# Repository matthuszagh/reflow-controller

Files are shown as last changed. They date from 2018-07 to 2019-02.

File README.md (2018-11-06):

A reflow oven controller, based on Henrik Forsten's project whose source code is found
[here](https://github.com/Ttl/reflow-controller). More in-depth documentation can be found in the
documentation subdirectory. The microcontroller code heavily leverages the [LUFA USB framework
code](http://www.fourwalledcubicle.com/LUFA.php).

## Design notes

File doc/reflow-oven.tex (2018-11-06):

\documentclass[11pt,twoside,a4paper]{report}
\setlength\parindent{0pt}
\usepackage{fullpage}
\usepackage{hyperref}
\hypersetup{
    colorlinks=true,
    linkcolor=black,
    urlcolor=blue,
}
\usepackage{mathtools}
\usepackage{booktabs}
\usepackage{ltablex}
\usepackage{amssymb}
\usepackage{graphicx}
\usepackage{tabularx}
\usepackage{gensymb}
\usepackage{pdfpages}
\usepackage{amsmath}
\usepackage{bm}
\usepackage{listings}
\usepackage{color}
\usepackage{float}
\usepackage[makeroom]{cancel}
\DeclareMathOperator{\csch}{csch}
\setlength\fboxrule{.3mm}
\DeclarePairedDelimiter\ceil{\lceil}{\rceil}
\DeclarePairedDelimiter\floor{\lfloor}{\rfloor}

\definecolor{dkgreen}{rgb}{0,0.6,0}
\definecolor{gray}{rgb}{0.5,0.5,0.5}
\definecolor{mauve}{rgb}{0.58,0,0.82}

\lstset{frame=tb,
  showstringspaces=false,
  columns=flexible,
  frame=none,
  basicstyle={\small\ttfamily},
  numbers=left,
  xleftmargin=.67cm,
  keywordstyle=\color{blue},
  commentstyle=\color{dkgreen},
  stringstyle=\color{mauve},
  breaklines=true,
  breakatwhitespace=true,
  tabsize=4
}

\def\dbar{{\mathchar'26\mkern-12mu d}}

\begin{document}

\tableofcontents

\section{Reflow Oven}

\subsection{Introduction}

\textit{Status: Functional}\newline

To do:
\begin{enumerate}
\item Review and understand microcontroller code.
\item Review and understand pc code.
\end{enumerate}

Building a homemade reflow oven will serve several benefits: (1) it will allow me to make PCBs in
the future with greater accuracy and less development time, and (2) it will give me a sense of how
to program, interact with and generally use microcontrollers to build embedded computers that have
less demanding performance constraints than is required when FPGAs are needed. FPGAs are often
overkill and many things can be done with a simple and cheap microcontroller. Additionally,
microcontrollers can often be used as a way to interface between an FPGA and a host computer.

\subsection{Materials \& Overview}

\subsubsection{Repository}
The repository for this project is at
\href{run:/home/matt/developer/reflow-controller}{/home/matt/developer/reflow-controller}. It
includes hardware design files as well microcontroller and host computer code. This project is taken
from Henrik Forsten, documented online
\href{http://hforsten.com/toaster-oven-reflow-controller.html}{here}.

\subsubsection{Hardware}
In addition to the materials specified by the hardware files, this also requires an ISP programmer
which is necessary to set fuse bits on the AVR microcontroller and also makes programming it
easier. The programmer can also be used in the future on any further AVR microcontroller. I am using
\href{https://www.sparkfun.com/products/9825}{this one}. The ISP uses an SPI interface to configure
the ATMega8U2 microcontroller. One of these pins is VCC that can be used to feed a 5V power supply
from the ISP to the reflow board. This feature can be toggled on and off using the power target
switch shown in Figure~\ref{fig:isp-power-switch}. Since that power line also connects to the
thermocouple ADC which can only support a max voltage of 4V, we must ensure that the power switch is
set to ``No Power'' before connecting the ISP to the AVR. In retrospect, it would have been much
better to route the header to VBUS instead of VCC which would have allowed us to use the ISP to
power the device.

\begin{figure}[h]
  \centering
  
  \caption{The ISP power switch. ``Power Target'' will route 5V to the AVR and ``No Power'' will not
    route a signal to the AVR.}
  \label{fig:isp-power-switch}
\end{figure}

\subsubsection{Microcontroller Software}
Programming the AVR is done with \href{http://www.fourwalledcubicle.com/LUFA.php}{LUFA}, which in
turn depends on \href{https://www.nongnu.org/avrdude/}{AVRDUDE} and
\href{https://dfu-programmer.github.io/}{DFU-Programmer} as well as
\href{https://www.microchip.com/webdoc/AVRLibcReferenceManual/index.html}{AVR Libc}. The AVR code
uses a PID controller to control the operation of a solid state relay attached to the oven (PWM) and
attempts to converge the measured temperature to the target temperature at each time instant.

\subsubsection{Host Computer Software}
The host computer code is written in Python (don't forget to activate the VirtualENV environment
when using it) in the code repository. It listens at the serial port /dev/ttyACM0 and plots the
temperature readings from the AVR. It isn't strictly necessary, but is very useful especially since
the oven is too slow to match the temperature profile and some additional interactive steps must be
taken such as insulating the oven and opening the door during cool-down.

\subsection{Methods}

\subsubsection{Schematic}
The schematic for the controller is shown in Figure~\ref{fig:reflow-controller-sch}. The main
component on this board is an
\href{http://ww1.microchip.com/downloads/en/DeviceDoc/doc7799.pdf}{ATMega8u2 microcontroller} from
Atmel. The microcontroller has built-in support for USB communication and 8k bytes of flash
memory. It is clocked by an 8MHz external clock (which is necessary for USB functionality) and is
powered at 3.3V. In order to correctly power the device we externally supply the power in one of 2
ways: (1) connect a 5V supply to VBUS via the J5 connector, or (2) allow the host PC to provide the
5V over the USB connection. The second alternative should be preferred in most scenarios, since we
will generally plot the output of the PID controller to the host computer. In both instances, the 5V
power supply is downregulated via an onboard regulator,
\href{https://www.diodes.com/assets/Datasheets/AP2127.pdf}{AP2127K}, to the 3.3V used by the
microcontroller.\newline

\begin{figure}[h]
  \centering
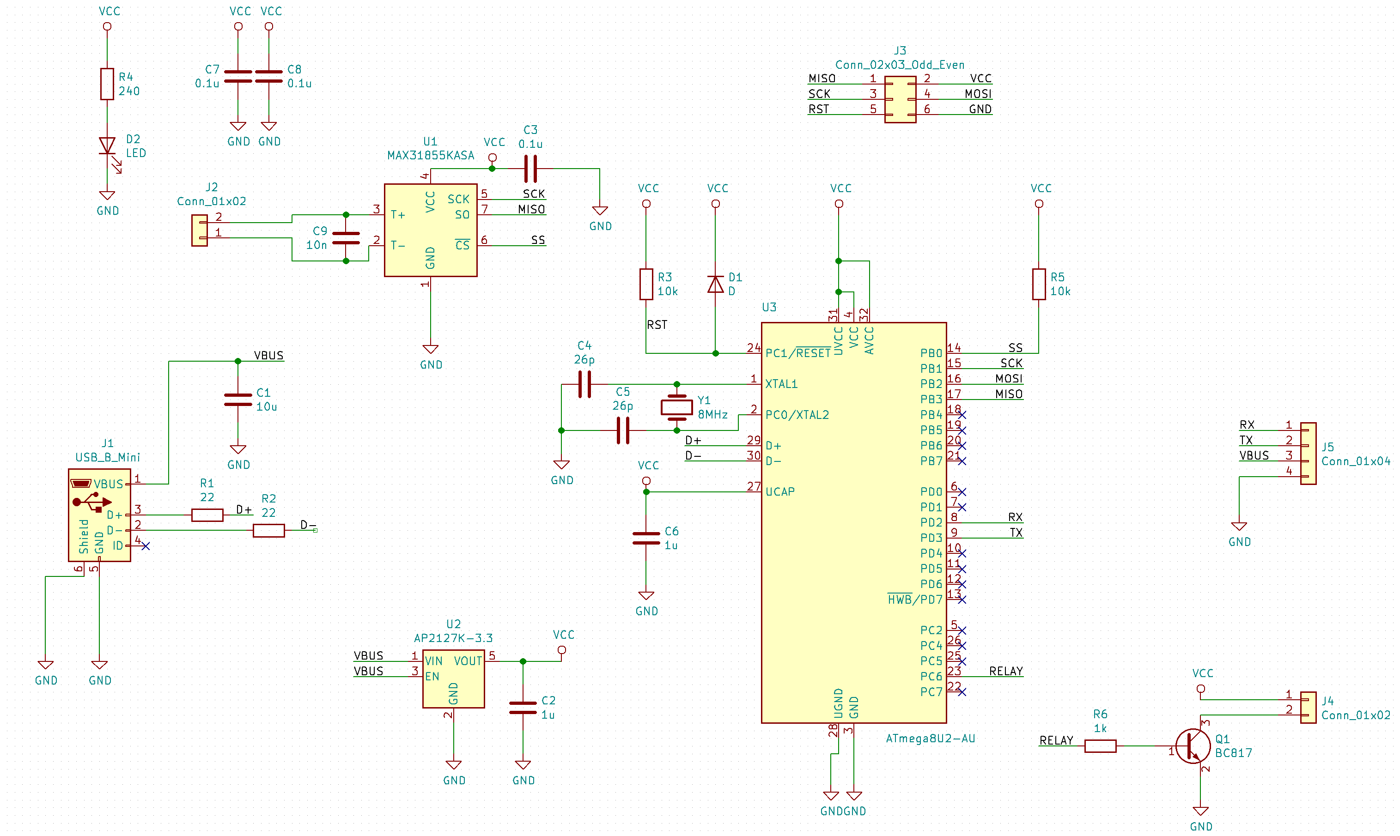
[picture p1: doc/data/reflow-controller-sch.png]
  
  \caption{Reflow controller schematic.}
  \label{fig:reflow-controller-sch}
\end{figure}

The microcontroller is also connected to a thermocouple ADC,
\href{https://datasheets.maximintegrated.com/en/ds/MAX31855.pdf}{MAX31855}, via an SPI interface
that reads out the temperature from inside the oven. To communicate with the thermocouple ADC, the
ATMega8U2 pulls the SS line low and drives the SCK (note that the maximum clock frequency allowed by
the thermocouple ADC is 5MHz). It then reads out the temperature from the thermocouple ADC
synchronized by the SCK clock signal. The 10nF capacitor placed between the T+ and T- pins filters
noise between the thermocouple lines and was strongly recommended by the datasheet.\newline

The microcontroller then communicates via an open collector to the solid state relay, which switches
the power supply to the oven. The open collector line is attached to the PC6 pin of the
microcontroller, which is the channel A output compare pin (OC1A) of the microcontroller's built-in
PWM module. An internal waveform generator combinationally compares an internal timer/counter value
to the output compare register, OCR1A, and generates a variable frequency output (PWM) on the PC6
pin. The method of operation for this is shown in Figure~\ref{fig:fast-pwm}. A register (TCNT1)
counts up from 0 to a top value specified by another register (ICR1) at a frequency specified by a
prescaler. Once it reaches the top value it returns back to 0. When the value of TCNT1 matches the
value of a compare register (OCR1A) also set by us and reset periodically, OC1A will be set (since
we are using an open collector configuration, this will set it to 0) and when it matches the value
of ICR1, it will be cleared (set to 1 in our case). The diagram shows that in addition to being able
to update the value of OCR1A, we can update the top value, ICR1, which can be used to update the
period of the PWM signal. However, we won't use this in our configuration. The PWM frequency is
given by Equation~\ref{eq:pwm-freq}, which, for our configuration ($f_{\text{clk}}=8\text{MHz}$,
$N=256$ and $\text{TOP}=6250$), gives a frequency of 5Hz.

\begin{figure}[h]
  \centering
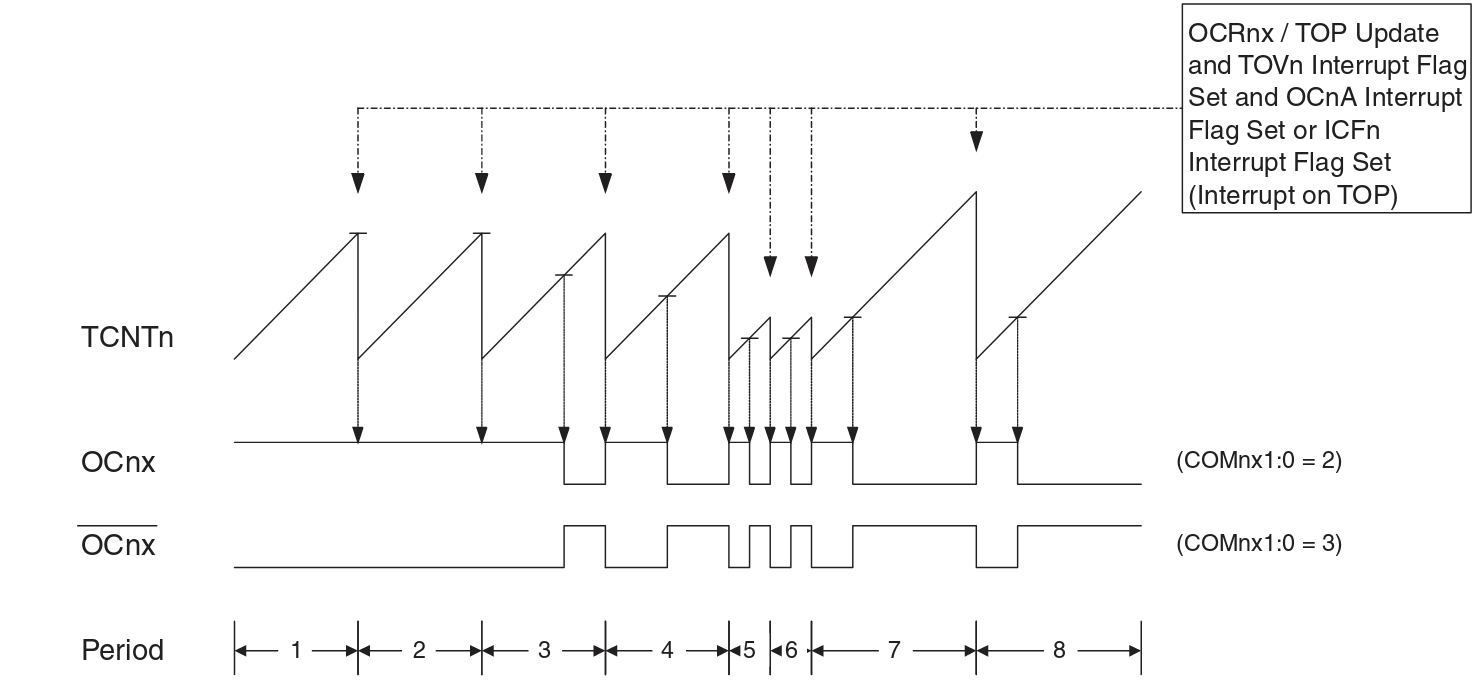
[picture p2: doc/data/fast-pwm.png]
  
  \caption{Fast PWM Mode timing diagram.}
  \label{fig:fast-pwm}
\end{figure}

\begin{equation}
  f_{\text{PWM}} = \frac{f_{\text{clk}}}{N \times (1 + \text{TOP})}
  \label{eq:pwm-freq}
\end{equation}

Finally, there is an additional connector (J3) that allows an ISP to configure the device.

\subsubsection{Microcontroller Software}
The microprocessor code depends heavily on the LUFA library and also includes several headers from
the AVR C standard library (\href{http://www.nongnu.org/avr-libc/}{Home Page} and
\href{http://www.nongnu.org/avr-libc/user-manual/index.html}{User Manual}). The LUFA USB.h header
file contains information about how to include the LUFA libraries and configure the ATMega8u2
microcontroller in order for it to enumerate and communicate correctly with a host computer. The
LUFA library allows several different configurations for the USB device, which correspond to
specific device drivers used by the host computer. The supported device classes are Android Open
Accessory, Audio 1.0, CDC-ACM, HID, MIDI, Mass Storage, Printer, RNDIS, and Still Image. Android
Open Accessory is for Android accessory devices, audio 1.0 is for audio devices such as microphones,
HID is for human interface devices such as keyboard and mice, MIDI is Musical Instrument Digital
Interface, Mass Storage is for USB storage devices, Printer is for printers, RNDIS is for network
devices attached to a USB bus, and Still Image is for digital cameras. Clearly, none of these are
relevant to our application. The only remaining device class is CDC-ACM, which can be used to
emulate serial ports over USB and transfer data between a host computer and a peripheral USB
device. This is the device class that we will use. It is worth noting that our microcontroller will
be acting as a device with a virtual serial port instead of as a device with a typical USB port,
even though the physical signals will still be transmitted over a USB cable and according to the USB
protocol. Although ACM seems to have been originally intended for modems and ISDNs, it is often used
for general data communication between a host computer and USB device, which matches our
application.\newline

LUFA defines a standard protocol that must be followed to correctly configure any device class. The
first step is to instantiate the ClassInfo struct (for our CDC device this is
\lstinline{USB_ClassInfo_CDC_Device_t}). The ClassInfo struct has two sections: a config section and
a state section. The config section must be fully specified in order to use the class driver. This
includes \lstinline{ControlInterfaceNumber}, \lstinline{DataINEndpoint},
\lstinline{DataOUTEndpoint}, and \lstinline{NotificationEndpoint}. This struct will be passed to
each of the driver's functions as the \lstinline{CDCInterfaceInfo} parameter. The code can be
adapted directly from the example provided by LUFA in the VirtualSerial demo. We must also copy the
LUFA directory from the root directory of the LUFA project and Config from the directory of the
VirtualSerial demo project to our microcontroller code directory.

\subsubsection{ATmega8U2 Configuration}
The ATmega8u2 AVR microcontroller comes preconfigured to use an internal oscillator rather than the
external crystal that I hooked up. This \href{http://www.engbedded.com/fusecalc/}{PalmAVR website}
can be used to set proper configurations and determine the corresponding fuse bits. It is important
not to use the external clock setting (external crystal or oscillator is fine) since that means you
intend to use an external clock (not soldered on the same PCB) and can be unrecoverable (or at least
difficult to recover from). The AVR came with the fuse bits
\lstinline{lfuse=0x5e hfuse=0xd9 efuse=0xf4} set. The fuse bits are described on page 247 of the
microcontroller datasheet. A fuse bit value of 0 indicates the corresponding fuse is programmed
whereas a fuse bit value of 1 indicates that fuse is not programmed. The clocking options are shown
in Table~\ref{tab:device-clocking-options}. \lstinline{efuse} stands for Extended Fuse Byte, which
controls the operation of brown-out detection and booting. \lstinline{hfuse} stands for Fuse High
Byte and controls the operation of several different things, none of which need to be
changed. \lstinline{lfuse} stands for Fuse Low Byte, which controls the operation of the clock
source and divide and is the only fuse byte that we need to reprogram. The default setting uses a
low power crystal oscillator, and divides the clock by 8, to generate a 1MHz clock.\footnote{The
  datasheet contains a contradiction. On page 29 it says that the device ships with the default
  clock source set to the internal RC oscillator. However, on page 248 it says that it ships with
  the clock source set to a low power crystal oscillator, which is correct.} We want to use the full
swing crystal oscillator and turn off the divide by 8 fuse. All other settings can be kept. This
corresponds to \lstinline{1101_0110} or \lstinline{0xd6}. \textbf{\{START INCOMPLETE\}} I have
previously set this value to \lstinline{0xbf}, which worked, although I think the other setting is
better. \textbf{\{END INCOMPLETE\}} This can be done with the command

\begin{lstlisting}[mathescape]
avrdude -c usbtiny -p atmega8u2 -U lfuse:w:0xd6:m -U hfuse:w:0xd9:m -U efuse:w:0xf4:m
\end{lstlisting}

\begin{center}
\begin{tabular}{l c}
  \textbf{Device Clocking Option} & \textbf{CKSEL3:0} \\
  \hline
  Low Power Crystal Oscillator & 1111 - 1000 \\
  Full Swing Crystal Oscillator & 0111 - 0110 \\
  Reserved & 0101 - 0100 \\
  Reserved & 0011 \\
  Calibrated Internal RC Oscillator & 0010 \\
  External Clock & 0000 \\
  Reserved & 0001 \\
  \label{tab:device-clocking-options}
\end{tabular}
\end{center}

\subsubsection{Host Computer Software}

\subsubsection{Soldering Attempts}
This \href{https://learn.adafruit.com/usbtinyisp/help}{Adafruit} article and this
\href{https://learn.sparkfun.com/tutorials/pocket-avr-programmer-hookup-guide/discuss}{Sparkfun}
article contain debugging information for a USBTiny device.\newline

My first attempt at soldering this device failed. These were the symptoms. When I plugged the device
directly into the USB port of my computer, the LED lit up and the ATMega8U2 microcontroller was
recognized by my computer. Additionally, I was able to erase the device memory with the command

\begin{lstlisting}[mathescape]
dfu-programmer atmega8u2 erase
\end{lstlisting}

This seems to indicate that at least part of the microcontroller was correctly soldered, and the
crystal and USB connector were correctly soldered. However, when I connected the ISP programmer to
the computer and connected the ISP header to the reflow controller, specifying ``No Power'', the LED
still lit up. Additionally, when I then connected a power supply across VBUS and GND, the current
between VBUS and GND was 0 (this may be normal; I forget whether the same thing occurred with the
board that worked). When the board was just connected to the 5V power supply, the current was about
60mA, which I believe was the same as the old board that worked. When I attempted to test the
connection with the board with the terminal command

\begin{lstlisting}[mathescape]
avrdude -c usbtiny -p atmega8u2
\end{lstlisting}

I got the error

\begin{lstlisting}[mathescape]
Could not find USB device 0x1781/0xc9f
\end{lstlisting}

which is apparently an error with USB3.x. Sure enough, when I tried the same thing with my older
Linux computer (with USB2.x ports), I got a new error

\begin{lstlisting}[mathescape]
initialization failed, rc=-1
\end{lstlisting}

which means that the computer was able to communicate with the ISP, but the ISP in turn was not able
to communicate with the board. This seems to either indicate that parts of the microcontroller were
incorrectly soldered, or the pin header was incorrectly soldered. I imagine that it was an issue
with the microcontroller since it seemed straightforward to solder the pin headers, and when the
microcontroller was first soldered there were a significant number of solder bridges that I had to
fix. Fixing the solder bridges both exposed the microcontroller to prolonged heat and potentially
lead to an insufficient amount of solder on the pins, or oxidation on the pins.\newline

The other changes that I made from the original design are an LED connected to between VCC and GND,
I got rid of the PTC connected to VBUS, and I added a diode for the power-on-reset connection. None
of these should adversely affect the operation of the board, including the LED, which should route
about 4.6mA of current through the diode. I see no reason why this should be bad for the operation
of the rest of the board.\newline

The way to solve this seems to be to improve the process of solder paste application to the
board. Every time I have applied solder paste it has been in between the pads in addition to on the
pads. I think I am applying way too much paste, which is consistent with the large number of solder
bridges that result after reflow (and that some components are not flat on the board). Follow the
directions in the soldering technique section to prevent this. Do not proceed with component
placement if there is solder between the pads. The other thing to do is to always connect 5V between
VBUS and GND \textbf{before} connecting the reflow board to the ISP. I'm not 100\% sure this will
make a difference, but it should ensure that the board gets the correct power supply.

\subsection{Discussion}

\subsection{Time Spent}

\end{document}

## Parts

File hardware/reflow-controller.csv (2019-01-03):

Id | Designator | Package | Quantity | Designation | Supplier and ref
1 | R1,R2 | R_0603_1608Metric | 2 | 22
2 | MH1,MH2,MH3,MH4 | MountingHole_2.7mm_M2.5_Pad_Via | 4 | MountingHole_Pad
3 | J1 | USB_Micro-B_Amphenol_10103594-0001LF_Horizontal | 1 | USB_B_Micro
4 | J3 | PinHeader_2x03_P2.54mm_Vertical | 1 | Conn_02x03_Odd_Even
5 | C1 | C_0603_1608Metric | 1 | 10u
6 | C2,C6 | C_0603_1608Metric | 2 | 1u
7 | C3,C7,C8 | C_0603_1608Metric | 3 | 0.1u
8 | C4,C5 | C_0603_1608Metric | 2 | 26p
9 | C9 | C_0603_1608Metric | 1 | 10n
10 | D1 | D_SOD-323 | 1 | D
11 | D2 | LED_0603_1608Metric | 1 | LED
12 | J2 | TerminalBlock_Phoenix_MKDS-1,5-2_1x02_P5.00mm_Horizontal | 1 | Conn_01x02
13 | J4 | PinHeader_1x02_P2.54mm_Vertical | 1 | Conn_01x02
14 | J5 | PinHeader_1x04_P2.54mm_Vertical | 1 | Conn_01x04
15 | Q1 | SOT-23 | 1 | BC817
16 | R3,R5 | R_0603_1608Metric | 2 | 10k
17 | R4 | R_0603_1608Metric | 1 | 240
18 | R6 | R_0603_1608Metric | 1 | 1k
19 | U1 | SOIC-8_3.9x4.9mm_P1.27mm | 1 | MAX31855KASA
20 | U2 | SOT-23-5 | 1 | AP2127K-3.3
21 | U3 | TQFP-32_7x7mm_P0.8mm | 1 | ATmega8U2-AU
22 | Y1 | Crystal_SMD_HC49-SD | 1 | 8MHz

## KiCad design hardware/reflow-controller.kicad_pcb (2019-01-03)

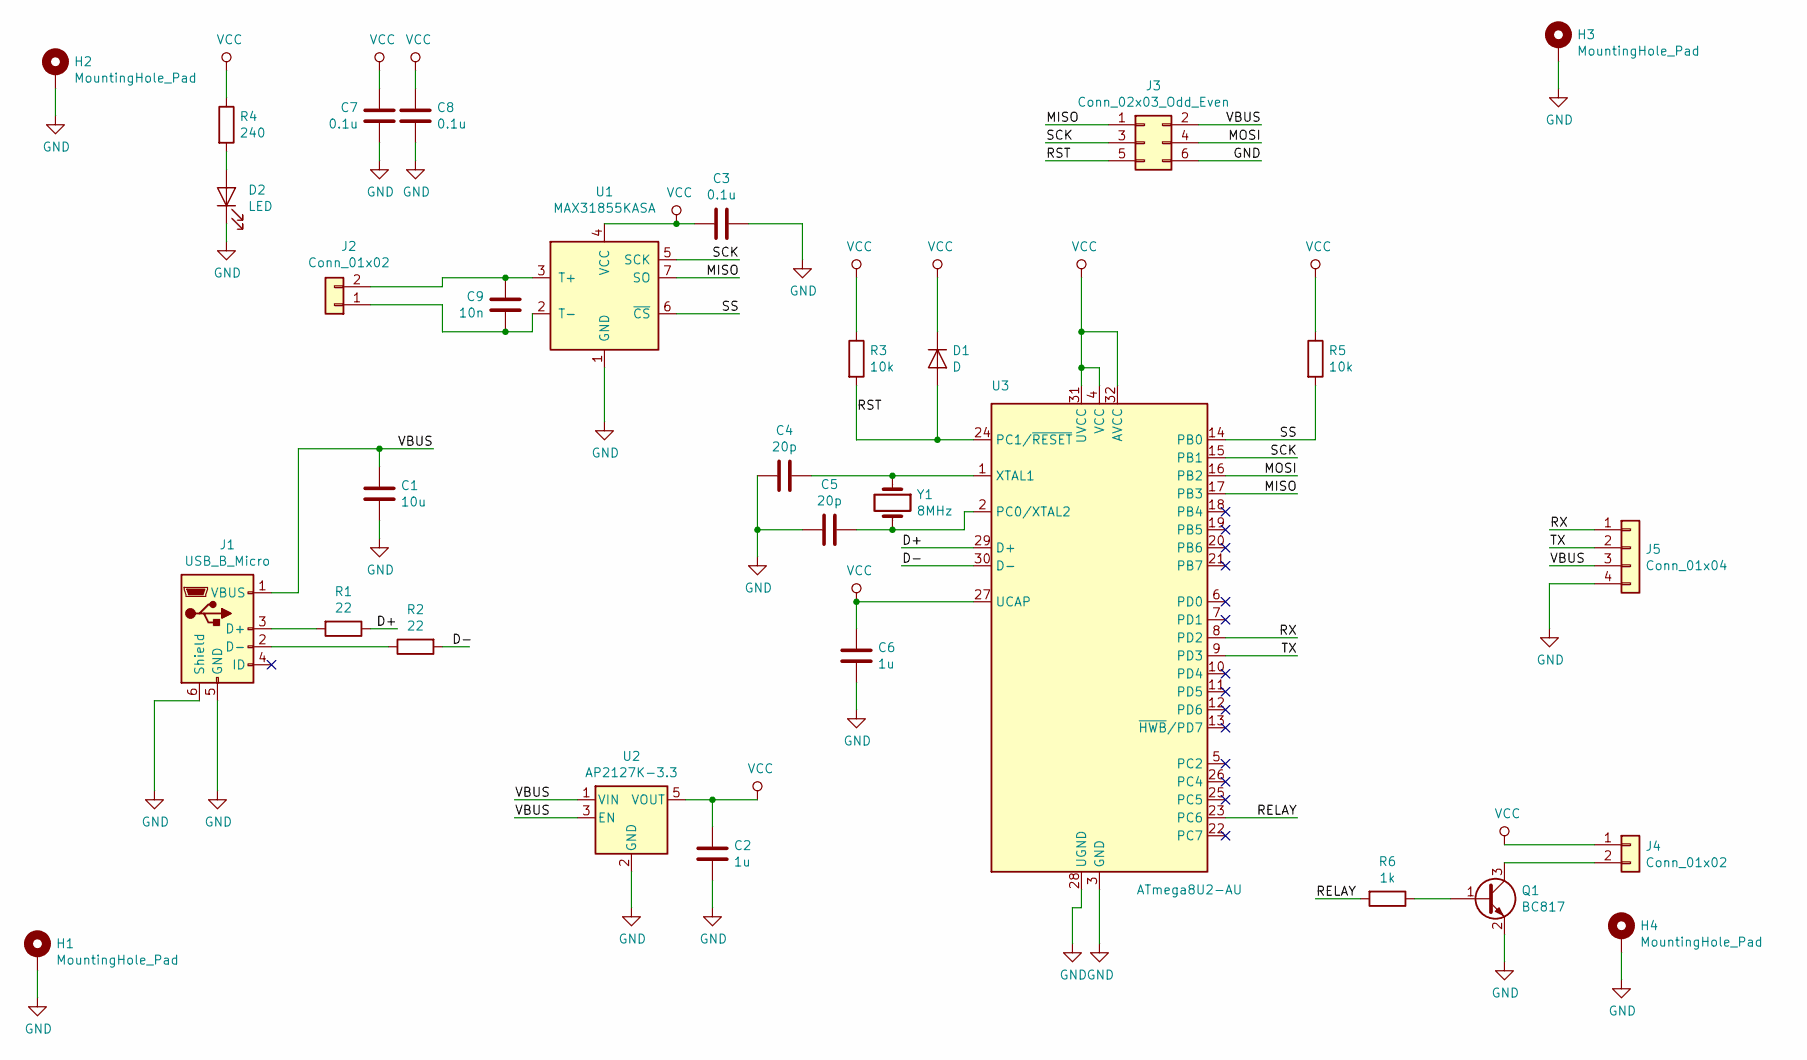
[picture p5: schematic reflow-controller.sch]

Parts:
C1: 10u; C_0603_1608Metric
C2, C6: 1u; C_0603_1608Metric
C3, C7, C8: 0.1u; C_0603_1608Metric
C4, C5: 20p; C_0603_1608Metric
C9: 10n; C_0603_1608Metric
D1: D; D_SOD-323
D2: LED; LED_0603_1608Metric
H1, H2, H3, H4: MountingHole_Pad; MountingHole_2.7mm_M2.5_Pad_Via
J1: USB_B_Micro; USB_Micro-B_Amphenol_10103594-0001LF_Horizontal
J2: Conn_01x02; TerminalBlock_Phoenix_MKDS-1,5-2_1x02_P5.00mm_Horizontal
J3: Conn_02x03_Odd_Even; PinHeader_2x03_P2.54mm_Vertical
J4: Conn_01x02; PinHeader_1x02_P2.54mm_Vertical
J5: Conn_01x04; PinHeader_1x04_P2.54mm_Vertical
Q1: BC817; SOT-23
R1, R2: 22; R_0603_1608Metric
R3, R5: 10k; R_0603_1608Metric
R4: 240; R_0603_1608Metric
R6: 1k; R_0603_1608Metric
U1: MAX31855KASA; SOIC-8_3.9x4.9mm_P1.27mm
U2: AP2127K-3.3; SOT-23-5
U3: ATmega8U2-AU; TQFP-32_7x7mm_P0.8mm
Y1: 8MHz; Crystal_SMD_HC49-SD

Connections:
/D+: R1.1, U3.29 (D+)
/D-: R2.2, U3.30 (D-)
/MISO: J3.1, U1.7 (SO), U3.17 (PB3)
/MOSI: J3.4, U3.16 (PB2)
/RELAY: R6.2, U3.23 (PC6)
/RST: D1.2 (A), J3.5, R3.2, U3.24 (PC1/~RESET)
/RX: J5.1, U3.8 (PD2)
/SCK: J3.3, U1.5 (SCK), U3.15 (PB1)
/SS: R5.2, U1.6 (~CS~), U3.14 (PB0)
/TX: J5.2, U3.9 (PD3)
/VBUS: C1.1, J1.1 (VBUS), J3.2, J5.3, U2.1 (VIN), U2.3 (EN)
GND: C1.2, C2.2, C3.1, C4.2, C5.2, C6.2, C7.2, C8.2, D2.1 (K), H1.1, H2.1, H3.1, H4.1, J1.5 (GND), J1.6 (Shield), J3.6, J5.4, Q1.2 (E), U1.1 (GND), U2.2 (GND), U3.3 (GND), U3.28 (UGND)
unnamed: C4.1, U3.1 (XTAL1), Y1.1
unnamed: C5.1, U3.2 (PC0/XTAL2), Y1.2
unnamed: C9.1, J2.2, U1.3 (T+)
unnamed: C9.2, J2.1, U1.2 (T-)
unnamed: D2.2 (A), R4.2
unnamed: J1.2 (D-), R2.1
unnamed: J1.3 (D+), R1.2
unnamed: J4.2, Q1.3 (C)
unnamed: Q1.1 (B), R6.1
VCC: C2.1, C3.2, C6.1, C7.1, C8.1, D1.1 (K), J4.1, R3.1, R4.1, R5.1, U1.4 (VCC), U2.5 (VOUT), U3.4 (VCC), U3.27 (UCAP), U3.31 (UVCC), U3.32 (AVCC)

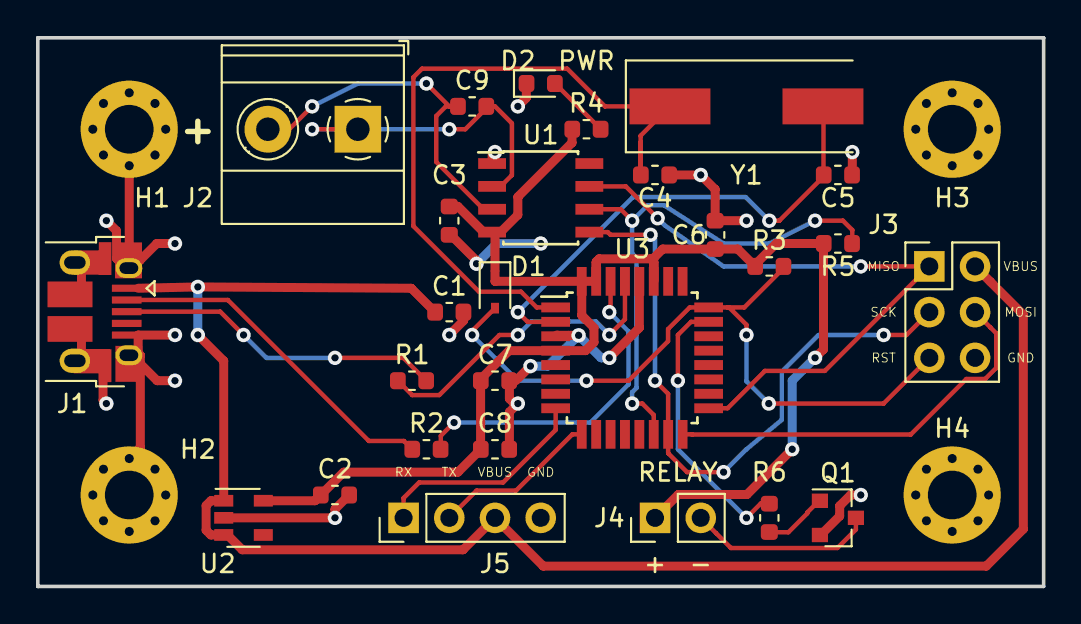
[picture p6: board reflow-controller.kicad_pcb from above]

Board: 2 copper layers, 55.9 x 30.5 mm, 31 parts (0 on the bottom side), 22 nets.

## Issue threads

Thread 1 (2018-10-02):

Controller should be able to sink power from the ISP when it is being programmed.

matthuszagh, 2018-10-02:
The ISP I'm using is the USBTiny which can can source 5V.

matthuszagh, 2018-10-03:
Fixed.

matthuszagh, 2018-10-03:
Completed in v2.0.

Closed 2018-10-03.

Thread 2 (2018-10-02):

Replace Mini USB connection with Micro.

matthuszagh, 2018-10-02:
Micro has better insertion cycle lifetime.

matthuszagh, 2018-10-03:
Completed in v2.0.

Closed 2018-10-03.

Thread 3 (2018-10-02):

Design should have mounting holes.

matthuszagh, 2018-10-02:
This way a case can be built for it.

matthuszagh, 2018-10-03:
Fixed

matthuszagh, 2018-10-03:
Fixed #3

matthuszagh, 2018-10-03:
fixes #3

matthuszagh, 2018-10-03:
Completed in v2.0.

Closed 2018-10-03.

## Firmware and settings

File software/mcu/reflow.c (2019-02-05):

#include "reflow.h"
#define SS 0
#define SCK 1
#define MOSI 2
#define MISO 3

static volatile bool update_pid = 0;
static volatile bool usb_connected = 0;

static uint16_t room_temp = 0;
static uint16_t prev_target = 0;
static profile_t profile;
static profile_t EEMEM eeprom_profile = {.start_rate = 1 * 4,
					 .soak_temp1 = 100 * 4,
					 .soak_temp2 = 110 * 4,
					 .soak_length = 100,
					 .peak_temp = 200 * 4,
					 .time_to_peak = 80,
					 .cool_rate = 2 * 4,
					 .pid_p = 360,
					 .pid_i = 80,
					 .pid_d = 0};

static state_enum reflow_state;
static int16_t integral = 0;
static int16_t last_error = 0;
static int8_t PID_debug = 0;

static FILE USBSerialStream;

USB_ClassInfo_CDC_Device_t VirtualSerial_CDC_Interface = {
	.Config =
		{
			.ControlInterfaceNumber = 0,
			.DataINEndpoint =
				{
					.Address = CDC_TX_EPADDR,
					.Size = CDC_TXRX_EPSIZE,
					.Banks = 1,
				},
			.DataOUTEndpoint =
				{
					.Address = CDC_RX_EPADDR,
					.Size = CDC_TXRX_EPSIZE,
					.Banks = 1,
				},
			.NotificationEndpoint =
				{
					.Address = CDC_NOTIFICATION_EPADDR,
					.Size = CDC_NOTIFICATION_EPSIZE,
					.Banks = 1,
				},
		},
};

void set_profile(void)
{
	/* Read profile from EEPROM to RAM */
	eeprom_read_block(&profile, &eeprom_profile, sizeof(profile));
}

void write_profile(void)
{
	/* Read profile from PC and replace current profile in RAM and EEPROM */
	uint8_t settings[20];
	uint8_t i = 0;
	int ReceivedChar;
	for (;;) {
		if ((ReceivedChar = fgetc(&USBSerialStream)) != EOF) {
			settings[i++] = (uint8_t)ReceivedChar;
			if (i == sizeof(profile))
				break;
		}
	}

#define TOU16(x, k) ((((uint16_t)x[k]) << 8) | ((uint16_t)x[k + 1]))

	/* Change the current settings in RAM */
	profile.start_rate = TOU16(settings, 0);
	profile.soak_temp1 = TOU16(settings, 2);
	profile.soak_temp2 = TOU16(settings, 4);
	profile.soak_length = TOU16(settings, 6);
	profile.peak_temp = TOU16(settings, 8);
	profile.time_to_peak = TOU16(settings, 10);
	profile.cool_rate = TOU16(settings, 12);
	profile.pid_p = TOU16(settings, 14);
	profile.pid_i = TOU16(settings, 16);
	profile.pid_d = TOU16(settings, 18);
	/* Write all settings as one block */
	eeprom_update_block(&profile, &eeprom_profile, sizeof(profile));
}

void output_profile(void)
{
	/* Print current profile through USB */
	fprintf(&USBSerialStream, "!%u,%u,%u,%u,%u,%u,%u,%u,%u,%u\n", profile.start_rate,
		profile.soak_temp1, profile.soak_temp2, profile.soak_length, profile.peak_temp,
		profile.time_to_peak, profile.cool_rate, profile.pid_p, profile.pid_i,
		profile.pid_d);
}

/* Get the target temperature */
uint16_t target_temp(uint16_t temp, uint16_t *timer)
{
	uint16_t target = 0;
	switch (reflow_state) {
	case (T_STOP):
		target = 0;
		break;
	case (T_START):
		target = prev_target + profile.start_rate;
		/* Clamp the target value and avoid it getting too big, if the oven
		 * isn't yet on. */
		target = CLAMP(target, room_temp,
			       MIN(profile.soak_temp1, temp + profile.start_rate * 5));
		if (temp > profile.soak_temp1 - 4 * 5) {
			*timer = 0;
			reflow_state = T_SOAK;
		}
		break;
	case (T_SOAK):
		/* Linear interpolation from soak_temp1 to soak_temp2 in soak_length
		 * seconds */
		if ((*timer) < profile.soak_length) {
			target = profile.soak_temp1 +
				 ((*timer) * (profile.soak_temp2 - profile.soak_temp1)) /
					 profile.soak_length;
		} else {
			target = profile.soak_temp2;
			if (temp > profile.soak_temp2 - 4 * 10) {
				*timer = 0;
				reflow_state = T_PEAK;
			}
		}
		break;
	case (T_PEAK):
		if ((*timer) < profile.time_to_peak) {
			target = profile.soak_temp2 +
				 ((*timer) * (profile.peak_temp - profile.soak_temp2)) /
					 profile.time_to_peak;
		} else {
			target = profile.peak_temp;
			if (temp > target) {
				*timer = 0;
				integral = 0; /* Zero integral term of PID for faster response */
				reflow_state = T_COOL;
			}
		}
		break;
	case (T_COOL):
		target = prev_target - profile.cool_rate;
		if (target < room_temp) {
			reflow_state = T_STOP;
		}
		break;
	default:
		/* Invalid state */
		reflow_state = T_STOP;
		break;
	}
	prev_target = target;
	return target;
}

void usb_rx(void)
{
	/*  Handle messages from host */
	char ReceivedChar;
	int ReceivedByte;
	/* Start commands with '!' */
	if ((ReceivedChar = fgetc(&USBSerialStream)) != '!') {
		return;
	}
	/* Get the real command */
	while ((ReceivedByte = fgetc(&USBSerialStream)) == EOF)
		;
	ReceivedChar = (char)ReceivedByte;
	/* PID debugging, prints PID term values */
	if (ReceivedChar == 'D') {
		PID_debug = 1;
	}
	if (ReceivedChar == 'd') {
		PID_debug = 0;
	}
	/* Write temperature profile and PID settings */
	if (ReceivedChar == 'W') {
		write_profile();
	}
	/* Start reflow */
	if (ReceivedChar == 'S') {
		reflow_state = T_START;
	}
	/* Stop reflow */
	if (ReceivedChar == 'H') {
		reflow_state = T_STOP;
	}
	/* Output current profile */
	if (ReceivedChar == 'O') {
		output_profile();
	}
	return;
}

uint16_t read_sensor(void)
{
	/* Bits:
	 * 31 : sign,
	 * 30 - 18 : thermocouple temperature,
	 * 17 : reserved(0),
	 * 16 : 1 if fault,
	 * 15 - 4 : cold junction temperature,
	 * 3 : reserved(0),
	 * 2 : 1 if thermocouple is shorted to Vcc,
	 * 1 : 1 if thermocouple is shorted to ground,
	 * 0 : 1 if thermocouple is open circuit */

	/* Enable slave */
	uint8_t sensor[4];
	uint16_t temp;
	int8_t i;
	/* SS = 0 */
	PORTB = (0 << SS);

	/* Wait for the device */
	_NOP();
	_NOP();
	/* Transmit nothing */
	for (i = 0; i < 4; i++) {
		SPDR = 0x00;
		/* Wait for transmission to complete */
		while (!(SPSR & _BV(SPIF)))
			;
		sensor[i] = SPDR;
	}

	/* Thermocouple temperature */
	if (sensor[0] & (1 << 7)) {
		/* Negative temperature, clamp it to zero */
		temp = 0;
	} else {
		temp = (((uint16_t)sensor[0]) << 6) + (sensor[1] >> 2);
	}

	/* Room temperature */
	if (sensor[2] & (1 << 7)) {
		/* Negative temperature, clamp it to zero */
		room_temp = 0;
	} else {
		room_temp = (((uint16_t)sensor[2]) << 4) + (sensor[3] >> 4);
		/* Sensor gives room temp as sixteenths of celsius,
		 * divide it by four to get quarters of celsius. */
		room_temp = room_temp / 4;
	}

	if (sensor[1] & 0x01) {
		/* Fault */
		fprintf(&USBSerialStream, "Fault:%u\n", sensor[3] & 0b00000111);
	}

	/* Disable slave */
	PORTB = (1 << SS);
	return temp;
}

void setupHardware(void)
{

	/* Disable wtachdog */
	MCUSR &= ~(1 << WDRF);
	wdt_disable();
	/* Disable prescaler */
	clock_prescale_set(clock_div_1);

	/* Set !SS and SCK output, all others input */
	DDRB = (1 << SS) | (1 << SCK);
	// bit_set(DDRB,SS);
	// bit_set(DDRB,SCK);
	bit_set(PORTB, SS); /* Set !SS high (slave not enabled) */
	bit_clear(PORTB, SCK);

	/* Set timer1 to count 1 second */
	TCNT1 = 0x00;
	/* PWM output to channel A, pin PC6 */
	TCCR1A = 0b10000010;
	/*  Set prescaler to divide by 256 for TMR1 */
	TCCR1B = 0b11011100;
	TIMSK1 = (1 << 2);
	ICR1 = _ICR1;
	OCR1B = 1;
	OCR1A = _ICR1;

	/* PC6 = Relay */
	DDRC = 0b01000000;
	PORTC = 0x00;
	DDRD = 0x00;

	/* Enable SPI, Master, set clock rate fck/2 */
	SPCR = (1 << SPE) | (1 << MSTR);
	SPSR = (1 << SPI2X);

	/* Initialize USB */
	USB_Init();
	CDC_Device_CreateStream(&VirtualSerial_CDC_Interface, &USBSerialStream);

	return;
}

/* Get PWM frequency from target temperature */
uint16_t approx_pwm(uint16_t target)
{
	int32_t t;
	t = ((_ICR1 * (target - room_temp)) / (MAXTEMP * 4));
	return (uint16_t)CLAMP(t, 0, _ICR1);
}

uint16_t pid(uint16_t target, uint16_t temp)
{
	int32_t error = (int32_t)target - (int32_t)temp;
	if (target == 0) {
		integral = 0;
		last_error = error;
		return 0;
	} else {

		int32_t p_term = profile.pid_p * error;
		int32_t i_term = integral * profile.pid_i;
		int32_t d_term = (last_error - error) * profile.pid_d;

		int16_t new_integral = integral + error;
		/* Clamp integral to a reasonable value */
		new_integral = CLAMP(new_integral, -4 * 100, 4 * 100);

		last_error = error;

		int32_t result = approx_pwm(target) + p_term + i_term + d_term;

		/* Avoid integral buildup */
		if ((result >= _ICR1 && new_integral < integral) ||
		    (result < 0 && new_integral > integral) || (result <= _ICR1 && result >= 0)) {
			integral = new_integral;
		}

		/* Clamp the output value */
		return (uint16_t)(CLAMP(result, 0, _ICR1));
	}
}

int main(void)
{

	uint8_t target_update = 0;
	bool tx_flag = 0;
	uint16_t temp = 0;
	uint16_t target = 0;
	uint16_t timer = 0; /* Timer for various reflow stages */

	setupHardware();
	set_profile();
	GlobalInterruptEnable();

	reflow_state = T_START;
	temp = read_sensor();
	target = target_temp(temp, &timer);
	timer++;

	while (1) {
		if (usb_connected) {
			/*  Check mail */
			usb_rx();
			CDC_Device_USBTask(&VirtualSerial_CDC_Interface);
			USB_USBTask();
		}

		if (usb_connected && tx_flag) {
			tx_flag = 0;
			/* Send temp temperature */
			fprintf(&USBSerialStream, "temp:%u,room:%u,target:%u,PWM:%u,state:%d", temp,
				room_temp, target, OCR1A, reflow_state);
			if (PID_debug)
				fprintf(&USBSerialStream, ",I:%d", integral);
			fprintf(&USBSerialStream, "\n");
		}
		if (update_pid) {
			/* Update target once per second */
			if (target_update++ == 5) {
				target_update = 0;
				target = target_temp(temp, &timer);
				timer++;
				tx_flag = 1;
			}
			/* Read the current temperature, updates temp and room_temp */
			temp = read_sensor();
			update_pid = 0;
			OCR1A = pid(target, temp);
		}
	}
}

ISR(TIMER1_COMPB_vect)
{
	/* Set PWM */
	update_pid = 1;
}

/** Event handler for the library USB Connection event. */
void EVENT_USB_Device_Connect(void) { usb_connected = 1; }

/** Event handler for the library USB Disconnection event. */
void EVENT_USB_Device_Disconnect(void) { usb_connected = 0; }

/** Event handler for the library USB Configuration Changed event. */
void EVENT_USB_Device_ConfigurationChanged(void)
{
	CDC_Device_ConfigureEndpoints(&VirtualSerial_CDC_Interface);
}

/** Event handler for the library USB Control Request reception event. */
void EVENT_USB_Device_ControlRequest(void)
{
	CDC_Device_ProcessControlRequest(&VirtualSerial_CDC_Interface);
}

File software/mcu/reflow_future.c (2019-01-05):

/* reflow.c
 *
 * The main source file for the reflow controller. This will both configure the
 * device to be used as a CDC ACM device and control the PID operation of the
 * toaster oven with a state machine.
 */

#include "reflow.h"

/** Port B pins. */
#define SS 0
#define SCK 1
#define MOSI 2
#define MISO 3

/** PWM parameters. */
#define TOP 6250

/** Temperature parameters. */
#define ROOM_TEMP 100

/** Temperature profile to load into EEPROM. Units are 1/4 of a degree C and 1
 * second. We use 1/4 of a degree since that is the temperature resolution of
 * the MAX31855 thermocouple ADC. The PID coefficients should be adjusted to
 * optimal values. `EEMEM` is an attribute that causes eeprom_profile to be
 * allocated in the .eeprom section.
 */
static profile_t EEMEM eeprom_profile = {.preheat_rate = 1 * 4,
                                         .soak_temp1 = 100 * 4,
                                         .soak_temp2 = 150 * 4,
                                         .soak_time = 90,
                                         .liquides_temp = 183 * 4,
                                         .time_to_liquides = 30,
                                         .peak_temp = 235 * 4,
                                         .time_to_peak = 60,
                                         .cool_rate = 2 * 4,
                                         .pid_p = 360,
                                         .pid_i = 80,
                                         .pid_d = 0};

static volatile bool usb_connected;
/** Update the PID every time the counter reaches its top value and resets. */
static volatile bool update_pid;
static bool
tx_flag; /** Set to 1 when we should transmit data to the host computer. */
/** Counts to 5 to update the target and flag that a transmission should be made
 * to the host computer. Since the period of a PWM waveform is 0.2s, this will
 * update the target and message the host every second. The OCR1A value will
 * still be updated every 0.2s but the target can only change at most once per
 * second and there is no need to inundate the host computer.
 */
static uint8_t target_update;
static profile_t profile;  /** Temperature profile in SRAM. */
static state reflow_state; /** Reflow state. */
static uint16_t room_temp; /** Room temperature. */
/** Target temperature. Initialize it to the starting temperature which is 25C.
 */
static uint16_t target = ROOM_TEMP;
static int16_t integral; /** Keeps track of the integral term of the PID. */
/** Keeps track of the previous error value for the derivative term of the PID.
 */
static int32_t prev_error;
static int8_t PID_debug = 0;

/** Standard file stream for the CDC interface when set up, so that the virtual
 * CDC COM port can be used like any regular character stream in the C APIs.
 */
static FILE USBSerialStream;

/** LUFA CDC Class driver interface configuration and state information. This
 * structure is passed to all CDC Class driver functions, so that multiple
 * instances of the same class within a device can be differentiated from one
 * another.
 */
static USB_ClassInfo_CDC_Device_t VirtualSerial_CDC_Interface = {
                                                                 .Config =
                                                                 {
                                                                  .ControlInterfaceNumber = 0,
                                                                  .DataINEndpoint =
                                                                  {
                                                                   .Address = CDC_TX_EPADDR,
                                                                   .Size = CDC_TXRX_EPSIZE,
                                                                   .Banks = 1,
                                                                  },
                                                                  .DataOUTEndpoint =
                                                                  {
                                                                   .Address = CDC_RX_EPADDR,
                                                                   .Size = CDC_TXRX_EPSIZE,
                                                                   .Banks = 1,
                                                                  },
                                                                  .NotificationEndpoint =
                                                                  {
                                                                   .Address = CDC_NOTIFICATION_EPADDR,
                                                                   .Size = CDC_NOTIFICATION_EPSIZE,
                                                                   .Banks = 1,
                                                                  },
                                                                 },
};

int main(void) {
        uint16_t temp = 0;
        uint16_t timer = 0; /* Timer for various reflow stages */

        setup_hardware();
        set_profile();
        GlobalInterruptEnable();

        reflow_state = PREHEAT;
        temp = read_temp();
        target = get_target(temp, &timer);
        timer++;

        while (1) {
                if (usb_connected) {
                        /*  Check mail */
                        usb_rx();
                        CDC_Device_USBTask(&VirtualSerial_CDC_Interface);
                        USB_USBTask();
                }

                if (usb_connected && tx_flag) {
                        tx_flag = 0;
                        /* Send temp temperature */
                        fprintf(&USBSerialStream, "temp:%u,room:%u,target:%u,PWM:%u,state:%d",
                                temp, room_temp, target, OCR1A, reflow_state);
                        if (PID_debug)
                                fprintf(&USBSerialStream, ",I:%d", integral);
                        fprintf(&USBSerialStream, "\n");
                }
                if (update_pid) {
                        /* Update target once per second */
                        if (target_update++ == 5) {
                                target_update = 0;
                                target = get_target(temp, &timer);
                                timer++;
                                tx_flag = 1;
                        }
                        /* Read the current temperature, updates temp and room_temp */
                        temp = read_temp();
                        update_pid = 0;
                        OCR1A = pid(target, temp);
                }
        }
}

void set_profile(void) {
        /* Read profile from EEPROM to RAM */
        eeprom_read_block(&profile, &eeprom_profile, sizeof(profile));
}
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

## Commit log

2018-06-22 Updated Makefile.
    [uuni.csv, uuni.sch]
2018-06-27 Kicad version of design.
    [reflow-controller-2018-06-07-13-18-05.sch, reflow-controller.kicad_pcb, reflow-controller.sch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]
2018-06-28 PCB passes DRC.
    [reflow-controller.kicad_pcb, reflow-controller.sch]
2018-06-29 PCB is complete and has been sent to fab.
2018-07-25 Updated microcontroller code.
    [reflow-controller.csv]
2018-07-25 PCB design complete and updated microcontroller code.
    [reflow-controller.csv]
2018-10-04 Fixed power supply when programmed by ISP, added mounting holes, replaced mini USB connector with micro connector.
    [reflow-controller.kicad_pcb, reflow-controller.sch]
2018-11-02 Fixed minimum values for solder mask clearance and width.
    [reflow-controller.csv, reflow-controller.kicad_pcb]
2018-11-04 Adjusted solder mask relief and rewrote PC code in C++.
    [reflow-controller.kicad_pcb, reflow-controller.sch]
2018-12-18 Improved solder mask dam size.
    [reflow-controller.kicad_pcb]
2019-01-03 Bom generation improvements.
    [reflow-controller.csv, reflow-controller.kicad_pcb, reflow-controller.sch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]
2019-01-05 Improved pc software and added MFN to schematic for USB receptacle.
    [reflow-controller.sch]
2019-02-05 Improved pc code.
    [reflow-controller.sch]
2019-09-23 Fix pc code and create reproducible Nix environment
    [Descriptors.h, pc.py]
